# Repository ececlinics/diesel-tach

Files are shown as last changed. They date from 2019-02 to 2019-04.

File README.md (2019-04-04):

# ECE Clinics: Diesel Tachometer
This is the main directory for the diesel tachometer project. The objective of this project is to design an adapter and mount for a diesel engine tachometer sensor. More specifically, the team is designing a better filter for the tachometer circuit. This repository will feature any and all code development for the project.

## Contents
* [Intro](#intro)
* [Directory](#directory)

# Intro
Most commercial vehicles on the road today have tachometers, but some diesel engine vehicles, such as older trucks or farm vehicles, do not. Many companies sell aftermarket diesel tachometers, which are the center focus of this project. Typical tachometers in gas engines may tap off the electrical signals from the spark plugs. However, since diesel engines instead use glow plugs which do not provide much useful data, diesel tachometers sense and measure using different methods. One method involves using magnetic pickup on the coil of the alternator.

# Directory
* [board](board/)
* [CAD files](CAD/)
* [code](code/)
* [docs](docs/)
* [scripts](scripts/)

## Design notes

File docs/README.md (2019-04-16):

# Documents
This subdirectory contains material related to the development of this project.

# Table of Contents
| Filename | Title | Description | Author |
|---|---|---|---|
|[msp430g2553.pdf](msp430g2553.pdf) |MSP430G2x53 MSP430G2x13 Mixed Signal Microcontroller |MSP430G2553 datasheet|Texas Instruments|
|[st-link-slsh-v2.pdf](st-link-slsh-v2.pdf)|ST-LINK/V2 in-circuit debugger/programmer for STM8 and STM32|ST-LINK/V2 databrief |ST |
|[stm8s001j.pdf](stm8s001j.pdf) |16MHz STM8S 8-bit MCU.... |STM8S001J3 datasheet |ST |
|[en.CD00190271.pdf](en.CD00190271.pdf) |STM8S and STM8AF Series 8-bit Microcontrollers |STM8S family guide |ST |
|[en.CD00194637.pdf](en.CD00194637.pdf) |Getting Started with STM8S and STM8AF Microcontrollers |STM8S developer guide|ST |
|[en.DM00026748.pdf](en.DM00026748.pdf) |ST-LINK/V2 in-circuit debugger/programmer for STM8 and STM32|ST-LINK/V2 user guide|ST |
|README.md |README |README |ECE Clinics Team |

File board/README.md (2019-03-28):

# board
This subdirectory contains PCB design files.

# Directory
* [MSP430G2553](MSP430G2553/)
* [STM8S001J3M3](STM8S001J3M3/)

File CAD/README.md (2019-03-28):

# CAD Files
This subdirectory contains CAD files for the project. We designed sensor mount and a case to house the PCB.

## Contents
* [Directory](#directory)
* [Software](#software)

# Directory
* tach_mount.SLDPRT
* tach_mount.STL

# Software
**SOLIDWORKS 2017-2018.** [Link to product page.](https://www.autodesk.com/products/inventor/overview)

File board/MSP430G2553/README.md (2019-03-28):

# MSP430G2553 PCB
This subdirectory contains PCB design files for the MSP430G2 board.

# Revisions
| Revision  | Description |
|---|---|
|[0](REV 0/)|Initial revision.|

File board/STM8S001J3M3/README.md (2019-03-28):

# STM8S001J3 PCB
This subdirectory contains PCB design files for the STM8S board.

# Revisions
| Revision | Description |
|---|---|
|[0](REV0_DieselTach_Filter_STM/)|Initial revision.|
|[1](REV1_DieselTach_Filter_STM/)| |

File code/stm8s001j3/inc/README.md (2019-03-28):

# stm8s001j3/inc

# Directory
* [iostm8s001.h](iostm8s001.h)
* [stm8s_conf.h](stm8s_conf.h)
* [stm8s_it.h](stm8s_it.h)

## iostm8s001.h
IO definition file for STM8S001 J3 devices, provided by COSMIC.

## stm8s_conf.h
Configuration file for STM8S which includes the appropriate peripheral header files from the [STM8S Standard Peripheral Driver Library](../STM8S_StdPeriph_Driver/) for the device.

## stm8s_it.h
Header file for [stm8s_it.c](../src/stm8s_it.c).

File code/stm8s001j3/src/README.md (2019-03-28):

# stm8s001j3/src

# Directory
* [stm8s_it.c](stm8s_it.c)

## stm8s_it.c
Main interrupt service routines for STM8S devices.

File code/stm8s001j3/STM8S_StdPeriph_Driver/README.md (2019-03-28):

# STM8S Standard Peripheral Driver Library
The STM8S Standard Peripheral Driver Library contains drivers for STM8S peripherals to aid in code generation. This folder contains several peripheral drivers useful for this project.

See the compiled help file for more information on the SPL.

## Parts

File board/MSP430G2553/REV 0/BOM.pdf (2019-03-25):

# | RefDes | Value | Name

1 | C1, C2 | NP | CAP_0603
2 | C3 | 0.1u | CAP_0603
3 | C4 | 0.1uF | CAP_0603
4 | C5 | 2.2u | CAP_0603
5 | C6 | 4.7u | CAP_0603
6 | D1, D2 | | SMAJ8
7 | D3 | | ?BZX84C3V3LT1G?
8 | D4 | | SMAJ16CA
9 | D5 | | DIODE_DO-214AC, SMA
10 | J1 | | EDSTLZ950/2
11 | J2 | | ?S3B-XH
12 | Q1 | | SSM3K37FS
13 | R1, R2, R16 | 6.8 | RES_0603
14 | R3, R4, R17, R18 | fuse | RES_1210
15 | R5, R8 | 4.7k | RES_0603
16 | R6, R9 | 1k | RES_0603
17 | R7 | 22k | RES_0603
18 | R10 | 2.4M | RES_0603
19 | R11, R15 | 10k | RES_0603
20 | R12, R14 | 1.5k | RES_0805
21 | R13 | 1.8k | RES_0603
22 | U1 | | FDC6306P
23 | U2 | | LT6015IS5#TRMPBF
24 | U3 | | TC2030-MCP
25 | U4 | | SPX1117
26 | U5 | | MSP430G2553IPW20R

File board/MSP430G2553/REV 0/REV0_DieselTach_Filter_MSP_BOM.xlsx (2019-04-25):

Index | Quantity | Part Number | Manufacturer Part Number | Description | Customer Reference | Available | Backorder | Unit Price | Extended Price USD
1 | 1 | 296-28430-1-ND | MSP430G2553IPW20R | IC MCU 16BIT 16KB FLASH 20TSSOP | U5 | 1 | 0 | 2.41 | 2.41
2 | 1 | BZX84C3V3LT1GOSCT-ND | BZX84C3V3LT1G | DIODE ZENER 3.3V 225MW SOT23-3 | D3 | 1 | 0 | 0.15 | 0.15
3 | 1 | 1016-1848-1-ND | SPX1117M3-L-3-3/TR | IC REG LINEAR 3.3V 800MA SOT223 | U4 | 1 | 0 | 0.45 | 0.45
4 | 1 | 1276-1085-1-ND | CL10A225KP8NNNC | CAP CER 2.2UF 10V X5R 0603 | C5 | 1 | 0 | 0.11 | 0.11
5 | 2 | RMCF0805JT1K50CT-ND | RMCF0805JT1K50 | RES 1.5K OHM 5% 1/8W 0805 | R12, R14 | 2 | 0 | 0.1 | 0.20
6 | 2 | 1276-1000-1-ND | CL10B104KB8NNNC | CAP CER 0.1UF 50V X7R 0603 | C3,C4 | 2 | 0 | 0.1 | 0.20
7 | 2 | RMCF0603JT10K0CT-ND | RMCF0603JT10K0 | RES 10K OHM 5% 1/10W 0603 | R11,R15 | 2 | 0 | 0.1 | 0.20
8 | 1 | RMCF0603JT1K80CT-ND | RMCF0603JT1K80 | RES 1.8K OHM 5% 1/10W 0603 | R13 | 1 | 0 | 0.1 | 0.10
9 | 1 | SSM3K37FSLFCT-ND | SSM3K37FS,LF | MOSFET NCH 20V 200MA SSM | Q1 | 1 | 0 | 0.24 | 0.24
10 | 1 | FDC6306PCT-ND | FDC6306P | MOSFET 2P-CH 20V 1.9A SSOT6 | U1 | 0 | 1 | 0.48 | 0.48
11 | 1 | LT6015IS5#TRMPBFCT-ND | LT6015IS5#TRMPBF | IC OPAMP GP 3.3MHZ RRO TSOT23-5 | U2 | 1 | 0 | 3.85 | 3.85
12 | 2 | RMCF0603JT1K00CT-ND | RMCF0603JT1K00 | RES 1K OHM 5% 1/10W 0603 | R6,R9 | 2 | 0 | 0.1 | 0.20
13 | 1 | RMCF0603JT2M40CT-ND | RMCF0603JT2M40 | RES 2.4M OHM 5% 1/10W 0603 | R10 | 1 | 0 | 0.1 | 0.10
14 | 2 | RMCF0603JT4K70CT-ND | RMCF0603JT4K70 | RES 4.7K OHM 5% 1/10W 0603 | R5,R8 | 2 | 0 | 0.1 | 0.20
15 | 1 | RMCF0603JT22K0CT-ND | RMCF0603JT22K0 | RES 22K OHM 5% 1/10W 0603 | R7 | 1 | 0 | 0.1 | 0.10
16 | 1 | 455-2250-ND | S3B-XH-A(LF)(SN) | CONN HEADER R/A 3POS 2.5MM | J2 | 1 | 0 | 0.22 | 0.22
17 | 4 | 507-1783-1-ND | 0ZCH0010FF2E | PTC RESET FUSE 60V 100MA 1210 | R3, R4, R17, R18 | 4 | 0 | 0.13 | 0.52
18 | 3 | RMCF0603JT6R80CT-ND | RMCF0603JT6R80 | RES 6.8 OHM 5% 1/10W 0603 | R1, R2, R16 | 3 | 0 | 0.1 | 0.30
19 | 2 | SMAJ8.0A-E3/61GICT-ND | SMAJ8.0A-E3/61 | TVS DIODE 8V 13.6V DO214AC | D1, D2 | 2 | 0 | 0.44 | 0.88
20 | 1 | SMAJ16CA-13FDICT-ND | SMAJ16CA-13-F | TVS DIODE 16V 26V SMA | D4 | 1 | 0 | 0.46 | 0.46
21 | 1 | ED1817-ND | EDSTLZ950/2 | TERM BLOCK HDR 2POS 90DEG 5.08MM | J1 | 1 | 0 | 0.87 | 0.87
22 | 1 | 1276-1903-1-ND | CL10A475MA8NQNC | CAP CER 4.7UF 25V X5R 0603 | C6 | 1 | 0 | 0.38 | 0.38
23 | 1 | B130-FDICT-ND | B130-13-F | DIODE SCHOTTKY 30V 1A SMA | D5 | 1 | 0 | 0.37 | 0.37

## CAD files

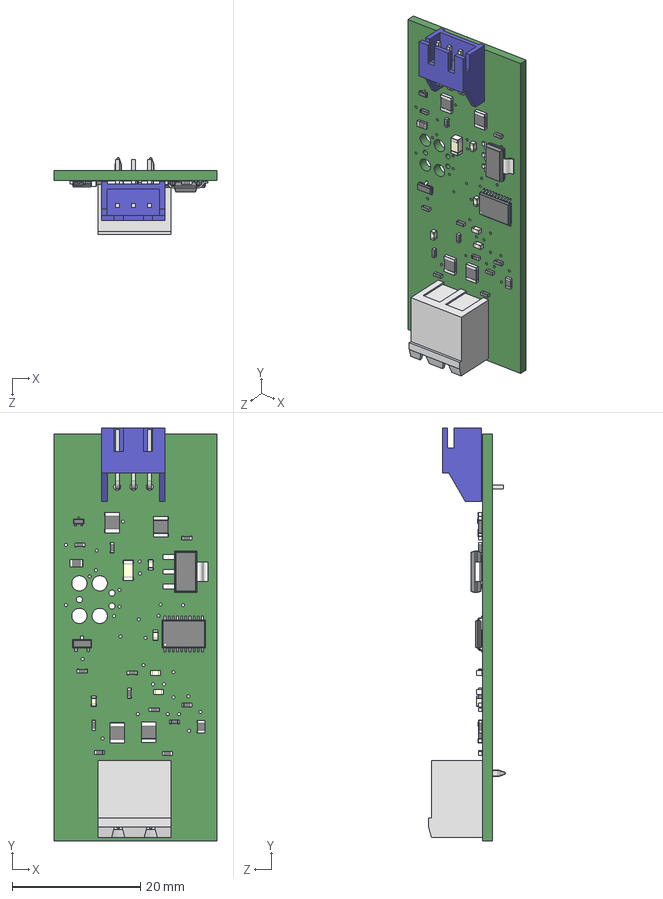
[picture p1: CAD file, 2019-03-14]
board/MSP430G2553/REV 0/3d Model.step
25.4 x 64.4 x 12.0 mm
Board_3d_Model
cap_0603 x 5
cap_1206
sot23
EDSTLZ950-2
S3B-XH-A
sot416
res_0603 x 12
res_1210 x 4
res_0805 x 2
sot223-4
tssop-20

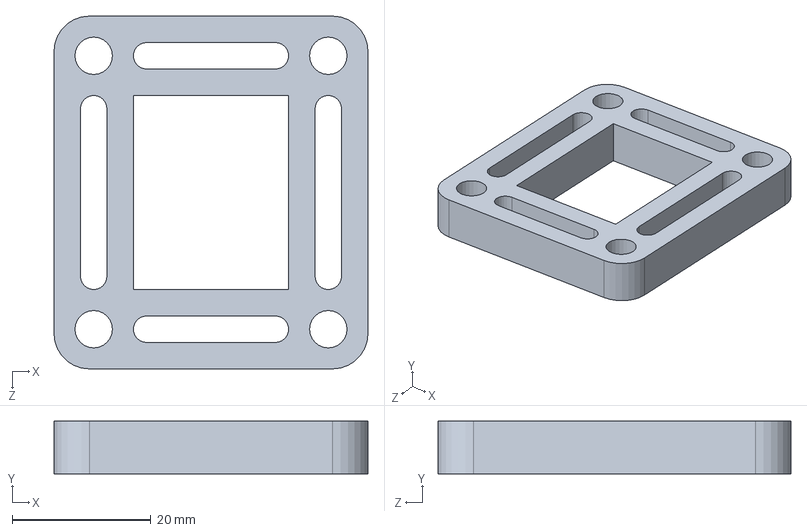
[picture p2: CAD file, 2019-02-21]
CAD/tach_mount.SLDPRT
45.2 x 7.62 x 50.8 mm

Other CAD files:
CAD/tach_mount.STL

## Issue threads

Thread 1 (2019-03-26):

STM Board

Chipable, 2019-03-26:
The following have been fixed on the MSP board but should also be done for the next revision of the STM board

1. 4.7uF capacitor should be a 0603 to match the BOM and save space
2. Pattern for the EDSTLZ950/2 needs to be updated with larger holes
3. SMAJ16CA-13-F should be ordered rather than SMLJ16A
4. Pads for SMAJ8.0A need to be corrected "larger"
5. Update BOM

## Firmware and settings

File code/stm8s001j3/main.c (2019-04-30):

/**
  ******************************************************************************
  * @file    main.c 
  * @author  Damon Boorstein
  * @date    24-Mar-2019
  * @brief   Main source file
   ******************************************************************************
  */ 


/* Includes ------------------------------------------------------------------*/
#include "stm8s.h"
#include "iostm8s001.h"
#include "binary_filt.h"

/* Private defines -----------------------------------------------------------*/
#define _GPIO 1
#define _TIM2 1
#define INITIAL_PULSE 0 // --- Damon 4/16/19: What's a good default PWM width? --- Damon 4/29/19: Using 0 for now
#define RELOAD_VALUE 0	// --- Damon 4/29/19: What's a good reload value for the watchdog?

/* Private function prototypes -----------------------------------------------*/
void resetGPIO(void);

/* Private functions ---------------------------------------------------------*/
void resetGPIO(void)
{
	GPIO_DeInit(GPIOA);
	GPIO_DeInit(GPIOB);
	GPIO_DeInit(GPIOC);
	GPIO_DeInit(GPIOD);
	GPIO_DeInit(GPIOE);
	GPIO_DeInit(GPIOF);
}

//uint8_t i = 0;
uint8_t period;

void main(void)
{
  disableInterrupts();
	/* ----- Damon 4/16/19: Need to enable/reset Independent Watchdog (IWDG) periph in this loop ----- */
	IWDG_SetReload();
	IWDG_ReloadCounter();
	
	// GPIO
	resetGPIO();
	PA_DDR |= GPIO_PIN_1;
	PA_DDR &= ~GPIO_PIN_0;
	
	// HSI (16MHz) CLK
	CLK_DeInit();
	CLK_SYSCLKConfig(CLK_PRESCALER_CPUDIV1);
	CLK_SYSCLKConfig(CLK_PRESCALER_HSIDIV1);
	CLK_ClockSwitchConfig(CLK_SWITCHMODE_AUTO, 
												CLK_SOURCE_HSI, 
												DISABLE, 
												CLK_CURRENTCLOCKSTATE_DISABLE);
	//CLK_HSICmd(ENABLE);
	
	// TIM2
	TIM2_DeInit();
	/* ----- Damon 4/16/19: This code was used for software PWM, we need HARDWARE PWM ------------------------
	TIM2_ITConfig(TIM2_IT_CC1, ENABLE);
	TIM2_SetCompare1(500);
	*/
	TIM2_PrescalerConfig(TIM2_PRESCALER_8, TIM2_PSCRELOADMODE_UPDATE);
	TIM2_PWMIConfig(TIM2_CHANNEL_1,							// Config PWM input on Channel 1
									TIM2_ICPOLARITY_RISING,			// polarity = rising edge
									TIM2_ICSELECTION_DIRECTTI,	// ----- Damon 4/29/19: I'm not sure about what type of polarity,
									TIM2_ICPSC_DIV8,						//					whether we need direct, or indirect, what divider we
									0);						//						//					need. I don't think we need a filter (I put 0 for that arg)
	TIM2_OC3Init( TIM2_OCMODE_PWM1,					// Initialize output on channel 3
								TIM2_OUTPUTSTATE_ENABLE,
								INITIAL_PULSE,						// INITIAL_PULSE = 0
								TIM2_OCPOLARITY_LOW);
	TIM2_SelectOCxM(TIM2_CHANNEL_3, TIM2_OCMODE_PWM1); // Select output compare mode PWM1 on channel 3 (pin 5)
	TIM2_CCxCmd(TIM2_CHANNEL_3, ENABLE); // Enable capture compare on channel 3
	TIM2_Cmd(ENABLE); // Enable TIM2
	/* ^--------------------------------------TIM2 hardware PWM----------------------------------------------^ */
	
	enableInterrupts();
	IWDG_Enable(); // enable IWDG
	
	/* Infinite loop */
  while (1)
  {
		// --- Damon 4/29/19: After interrupt, return here, set new pwm pulse width, enable TIM2 CH3
		// -----------------------------------------------------------------------------------------
		TIM2_CCxCmd(TIM2_CHANNEL_3, DISABLE); // disable channel 3
		TIM2_OC3Init( TIM2_OCMODE_PWM1,					// Initialize output on channel 3
									TIM2_OUTPUTSTATE_ENABLE,
									period,										// update pwm period with new period
									TIM2_OCPOLARITY_LOW);
		TIM2_CCxCmd(TIM2_CHANNEL_3, ENABLE); // re-enable CC on channel 3
		// ^---------------------------------------------------------------------------------------^
		
  }
  
}

#ifdef USE_FULL_ASSERT

/**
  * @brief  Reports the name of the source file and the source line number
  *   where the assert_param error has occurred.
  * @param file: pointer to the source file name
  * @param line: assert_param error line source number
  * @retval : None
  */
void assert_failed(u8* file, u32 line)
{ 
  /* User can add his own implementation to report the file name and line number,
     ex: printf("Wrong parameters value: file %s on line %d\r\n", file, line) */

  /* Infinite loop */
  while (1)
  {
  }
}
#endif

// ------ Damon 4/16/19: interrupt handler for TIM2 PWM --------
INTERRUPT_HANDLER(TIM2_OVR_IQRHandler,TIM2_OVR_UIF_vector)
{
	/*int*/ period = calc_period(dyn_window_filt(PA_ODR & GPIO_PIN_0));
	//int i;
	
	// software PWM
/*if(i >= period >> 1)
		GPIO_WriteLow(GPIOA, GPIO_PIN_1);
	else
		GPIO_WriteHigh(GPIOA, GPIO_PIN_1); */

	// increment i
	if(i > period - 1)
		i = 0;
	else
		i++;
		
	// --- Damon 4/29/19: clear TIM2 interupt flag here
}

/*****END OF FILE****/

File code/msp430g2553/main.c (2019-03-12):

/**
* @author Robert Page
* @date 2/21/2019
*/


#include <stdint.h>
#include <msp430.h>
#include "binary_filt.h"

uint8_t i = 0, period;

int main(void)
{
    WDTCTL = WDTPW | WDTHOLD;   // stop watchdog timer
    P1DIR |= BIT1; //1.1 data output
    P1DIR &= ~BIT0; //1.0 data input

    //16MHz clock
    BCSCTL1 = CALBC1_16MHZ; // Set range
    DCOCTL = CALDCO_16MHZ; // Set DCO step + modulation*/

    // TIMER INTERRUPT
    TA1CCTL0 = CCIE;                             // CCR0 interrupt enabled
    TA1CTL = TASSEL_2 + MC_1;           // SMCLK/8, upmode
    TA1CCR0 =  500;                     // 12.5 Hz

    _BIS_SR(CPUOFF + GIE);          // Enter LPM0 w/ interrupt

}

// Timer 1 A0 interrupt service routine
#pragma vector = TIMER1_A0_VECTOR
__interrupt void Timer1_A0_ISR( void ){
    period = calc_period(dyn_window_filt(P1IN & BIT0));

    // software PWM
    if(i>=period>>1)
        P1OUT &= ~BIT1;
    else
        P1OUT |= BIT1;

    //increment i
    if(i>period-1)
        i = 0;
    else
        i++;

    //P1OUT = (P1OUT & ~BIT1)|(dyn_window_filt(P1IN & BIT0)<<1 & BIT1);
}

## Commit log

2019-02-21 Adding 'CAD files'/
    [tach_mount.SLDPRT, tach_mount.STL]
2019-02-25 indexing error fixed, code passes bench test, ready for vehicle test
    [main.c]
2019-02-26 fixed overflow of pulse sum
    [main.c]
2019-02-26 Adding price quotes workbook
    [price_quotes.csv]
2019-02-28 change to the csv
    [price_quotes.csv]
2019-02-28 Updated quotes.
    [price_quotes.csv]
2019-02-28 Updated quotes
    [price_quotes.csv]
2019-02-28 Updating quotes and README.
    [price_quotes.csv]
2019-03-04 Renamed "CAD files" to "CAD" and updating README
    [tach_mount.SLDPRT, tach_mount.STL]
2019-03-04 Updating gitignore and renaming 'dynamic filter' to 'dynamic-filter'
2019-03-06 Docs folder and datasheet for ST-LINK/V2. Removing price_quotes.csv
    [price_quotes.csv]
2019-03-12 removed pcb folder
2019-03-12 Recovered board files from dynamic
    [REV0_DieselTach_Filter_MSP.gbl, REV0_DieselTach_Filter_MSP.gbo, REV0_DieselTach_Filter_MSP.gbs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]
2019-03-12 Added STM8 files
    [REV0_DieselTach_Filter_STM_BOM.xlsx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]
2019-03-12 updated with 3d models
    [3d Model.step]
2019-03-14 updeated component models
    [3d Model.step]
2019-03-25 PCB files, excluding gerbers, updated with correct C6 size of 0603
    [BOM.csv]
2019-03-25 updated schematic with tag-connect symbol
2019-04-02 STM PCB update
2019-04-04 Update to REV1 of the STM schematic
2019-04-16 Updating code. New files, including IWDG driver.
2019-04-22 BOM highlight
    [REV0_DieselTach_Filter_MSP_BOM.xlsx]
